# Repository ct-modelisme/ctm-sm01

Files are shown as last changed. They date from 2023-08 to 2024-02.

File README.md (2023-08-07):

# CTM-SM01: Servo-Motors decoder

The CTM-SM01 is a servo-motors electronic controller for modelrailway projects.
This electronic card is compatible with DCC & AC/DC train layouts.

## Licenses

The hardware is released under OpenHardware principes, and the software under OpenSource principes.

 - Hardware (PCB): [Creative Commons Attribution-ShareAlike 4.0 International License](http://creativecommons.org/licenses/by-sa/4.0/)
 - Software (Firmware): [GNU General Public License v3](https://www.gnu.org/licenses/)

## Current releases

 - Hardware (PCB): version 1.3
 - Software (Firmware): version 1.2

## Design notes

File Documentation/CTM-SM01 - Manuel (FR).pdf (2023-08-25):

# CTM-SM01

## Commande de servo-moteurs

La carte CTM-SM01 est une carte de commande pour 2 aiguillages actionnés par servo-moteur. Elle peut également être utilisée pour commander des signaux mécaniques ou passages à niveau là aussi actionnés par servo-moteur.
En cas de bogue, ou simplement si vous avez des suggestions, merci de me contacter à l’adresse : cyrille.toulet@linux.com

## Fonctionnalités

- Commande par DCC ou par boutons poussoirs (déportés ou non) ;
- 2 voies avec commandes et adresses DCC distinctes ;
- Relais pour réalimentation du cœurs d’aiguillage + option (TCO, rétro-signalisation, etc.) ;
- Fonctionnalité d’apprentissage manuel des débuts et fins de courses ;
- Fonctionnalité d’apprentissage dynamique des adresses DCC ;
- Connexion USB série 115 200 bauds (optionnelle).
https://www.ct-modelisme.fr/ | CTM-SM01 | PCB 1.3 – Firmware 1.2
| Page 1 | Révision : 25 août 2023

## Montage

## Aperçu du montage minimal

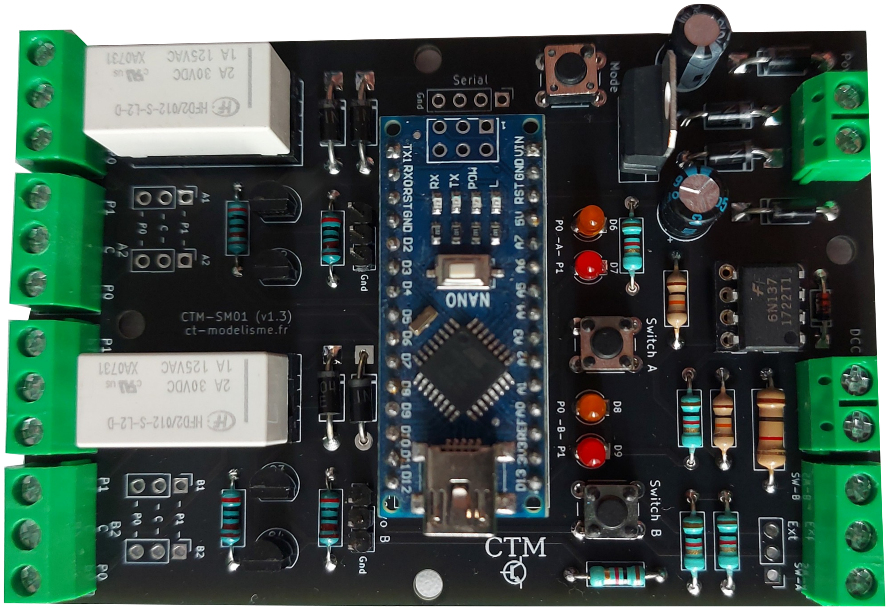
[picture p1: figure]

https://www.ct-modelisme.fr/ | CTM-SM01 | PCB 1.3 – Firmware 1.2
| Page 2 | Révision : 25 août 2023

## Liste des composants

Référence | Qté | Valeur | Type / Boitier / Pas | Autre
A1 | 1 | Arduino Nano
C1 | 1 | Condensateur 220µF / 25V | Radial / D=6.3mm / P=2.5mm
C2 | 1 | Condensateur 220µF / 16V | Radial / D=6.3mm / P=2.5mm
D1, D2, D3, D4, D10, D11, D12, D13 | 8 | Diode 1N4007
D5 | 1 | Diode 1N4148
D6, D8 | 2 | LED verte | 3mm | Ou n’importe quelle autre couleur
D7, D9 | 2 | LED rouge | 3mm | Ou n’importe quelle autre couleur
J1, J2 | 2 | Bornier à vis 1x2 | P=5.08mm
J3, J8, J9, J10, J11 | 5 | Bornier à vis 1x3 | P=5.08mm | Optionnel (si utilisation de J4, J12, J13, J14, J15)
J5 | 1 | Connecteur tulipe 1x4 broches | P=2.54mm | Optionnel (non implémenté pour le moment)
J4, J12, J13, J14, J15 | 5 | Connecteur tulipe 1x3 broches | P=2.54mm | Optionnel (si utilisation de J3, J8, J9, J10, J11)
J6, J7 | 2 | Connecteur 1x3 broches pour servo-moteur | P=2.54mm
K1, K2 | 2 | Relai bistable HFD2 012-S-L2
Q1, Q2, Q3, Q4 | 4 | Transistor BC547 | TO-92
R1 | 1 | Résistance 1k / 1W
R5, R6 | 2
R2, R3, R4, R7, R8 | 5
R9, R10, R11, R12 | 4
SW1, SW2, SW3 | 3 | Bouton poussoir à souder | 6mm
U1 | 1 | Opto-coupleur 6N137 | DIP-8
U2 | 1 | Régulateur de tension LM7805 | TO-220
PCB | 1 | Circuit imprimé CTM-SM01
Options recommandées | Qté | Valeur | Type / Boitier / Pas | Autre
A1 | 2 | Connecteur femelle 15 broches
K1, K2 | 2 | Support de CI 2x8 broches | DIP-16
U1 | 1 | Support de CI 2x4 broches | DIP-8

Résistance 10k / 0.25W
Résistance 1k / 0.25W
Résistance 2.2k / 0.25W

## Ordre de montage recommandé

Comme pour n’importe quel circuit électronique, faites attention au sens des composants (tous sauf les résistances) et commencez des composants les moins hauts pour terminer sur les plus hauts : diode 1N4148 (D5), puis résistances 1/4 W (toutes sauf R1), puis diodes 1N4007 (D1 à D4 et D10 à D13) et résistance 1W (R1). Ensuite, boutons poussoirs (SW1-3), supports de CI (s’il y en a), opto-coupleur (U1), LEDs, transistors BC547 (Q1 à Q4), connecteurs et borniers à vis, condensateurs 220µF (C1 et C2), relais (K1 et K2) et enfin, le régulateur de tension 5V (U2).

Aide complémentaire : si vous doutez du sens des LEDs, c’est la cathode (le côté plat de l’arrondi de la LED, qui est également le côté de la patte la plus courte) qui se trouve vers les écritures D5 à D9. Pour les transistors Q1 à Q4, faites bien attention de ne pas souder plusieurs pattes ensemble, car elles sont assez rapprochées. Enfin, faites bien attention lors de l’enfichage de l’opto-coupleur U1 et de l’arduino A1 de ne pas plier de patte.

## Options

En fonction du câblage de votre réseau, vous pouvez opter pour presque chaque entrée/sortie entre tiliser un bornier, utiliser un connecteur tulippe ou à broche, ou encore souder des fils directement à la place du connecteur.
Ainsi, les connecteurs J3 et J4 sont reliés, ainsi que J8 avec J12, J9 avec J13, J10 avec J14, et J11 avec J15.
Pour rendre démontable les relais ou l’arduino, vous pouvez également ajouter les supports femelles préconisés dans la liste des compostants.
https://www.ct-modelisme.fr/ | CTM-SM01 | PCB 1.3 – Firmware 1.2
| Page 4 | Révision : 25 août 2023

## Installation

## Firmware

Pour télécharger le dernier firmware de la carte CTM-SM01, rendez-vous sur le site, rubrique
« Téléchargements » : https://ct-modelisme.fr/
Compilez et envoyez le firmware de la carte vers un arduino nano à partir de du logiciel Arduino SDK. Puis enfichez l’arduino sur le connecteur A1.

## Fixation

La carte électronique dispose de 4 trous de montage M3 pour être fixée avec des vis ou des supports édhésifs.

## Connexions

- Connectez une alimentation de 12 à 15V DC sur le connecteur « Power » (peu importe la polarité).
- Connectez ensuite le bus JK sur le connecteur « DCC » (pas de polarité particulière non plus).
- Connectez le servo-moteur de l’aiguillage A sur le connecteur J6 (inscription « Servo A ») et le servo-moteur de l’aiguillage B sur le connecteur J7 (inscription « Servo B »).
Astuce : L’inscription « Gnd » correspond au fil de masse (généralement le fil marron ou noir) du servo-moteur.
- Si vous avez des boutons poussoirs de commande déportés (par exemple ceux d’un TCO), connectez les sur un des connecteurs SW-A / Ext / SW-B.
- Enfin, connectez votre cœur d’aiguille sur un commun (A1-C, ou A2-C, ou B1-C, ou B2-C) et le bus JK qui alimente l’aiguille sur les bornes correspondantes (ex : A1-P0 et A1-P1 si A1-C, ou A2-P0 et A2-P1 si A2-C, ou B1-P0 et B1-P1 si B1-C, ou B2-P0 et B2-P1 si B2-C).
- Le second contact de chaque relai peut être utilisé par exemple pour de la rétro-signalisation, ou pour alimenter des signaux de voie.
https://www.ct-modelisme.fr/ | CTM-SM01 | PCB 1.3 – Firmware 1.2
| Page 5 | Révision : 25 août 2023

## Aide visuelle

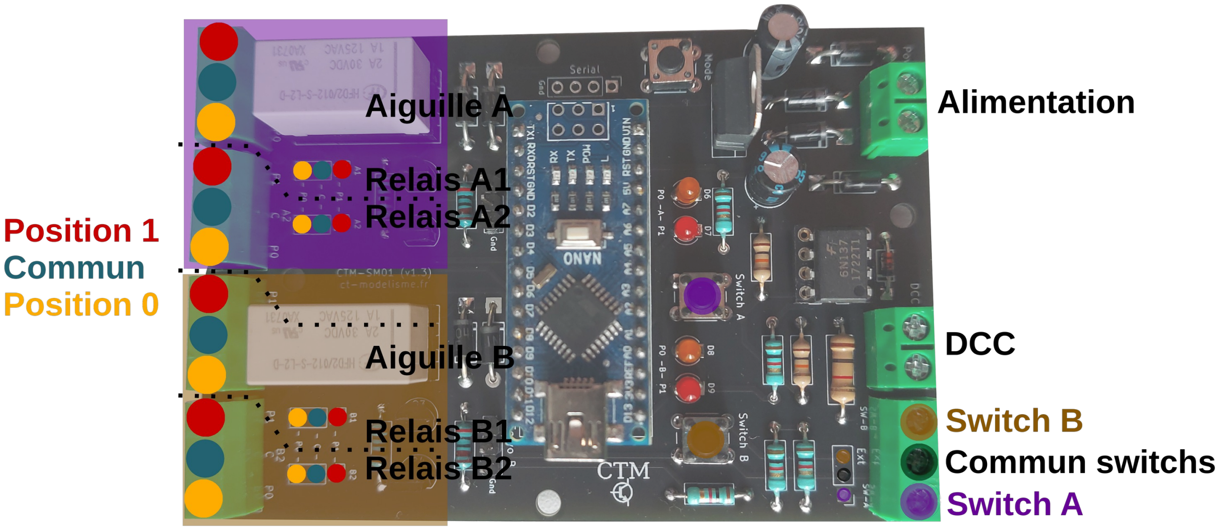
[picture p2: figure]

## Utilisation

## Apprentissage d’adresse DCC

Pour entrer en mode apprentissage d’adresse, appuyez 3 secondes sur le bouton « Mode ». La LED « L » de l’arduino s’allume.
Envoyez une commande d’accessoire sur la première adresse voulue depuis votre centrale DCC. Cette adresse sera mémorisée par la carte comme adresse DCC de l’aiguillage A.
Ensuite, envoyez une nouvelle commande d’accessoire sur la seconde adresse voulue. Cette seconde adresse sera mémorisée par la carte comme adresse DCC de l’aiguillage B.
Une fois les deux adresses apprises, la carte repasse en mode normal et la LED « L » de l’arduino s’éteint.
Astuce : vous pouvez quitter à tout moment le mode apprentissage en appuyant 2 secondes sur le bouton « Mode ».

## Réglage de début et fin de course des servo-moteurs

Pour entrer en mode apprentissage des positions, appuyez 2 secondes sur le bouton « Mode », puis sans le relacher, appuyez 2 secondes sur le bouton «Switch A ». Relâchez « Switch A » puis relachez « Mode ».
La première LED clignote. Vous allez régler la position de début de course du servo-moteur de l’aiguillage A en restant appuyé sur le bouton « Switch A » ou « Switch B ». Le servo-moteur se déplace en temps réel.
Une fois la position de début de course de l’aiguillage A réglée, appuyez 1 seconde sur le bouton « Mode ».
La seconde LED clignote. Vous allez régler la position de fin de course du servo-moteur de l’aiguillage A de la même manière que précédement.
Une fois la position de fin de course de l’aiguilage A réglée, appuyez 1 seconde sur le bouton « Mode ».
La troisième LED clignote, indiquant la configuration du début de course de l’aiguillage B. Procédez au réglage de la même manière que précédement.
Une fois la position de début de course de l’aiguillage B réglée, appuyez 1 seconde sur le bouton « Mode ».
La quatrième LED clignote, indiquant finalement la configuration de fin de course du servo-moteur de l’aiguillage B.
Une fois le réglage terminé, appuyez 1 seconde sur le bouton « Mode » pour revenir en
https://www.ct-modelisme.fr/ | CTM-SM01 | PCB 1.3 – Firmware 1.2
| Page 7 | Révision : 25 août 2023

fonctionnement normal.

## Moniteur série & réinitialisation de la carte

Lorsque vous branchez un câble USB à l’arduino, et que vous lancez le moniteur série à 115 200 bauds, un appuis court sur le bouton « Mode » imprimera la configuration courante de la carte. Différentes informations seront affichée suite à plusieurs appuis sur le bouton « Mode », jusqu’à revenir en fonctionnement normal.
Astuce : lors que vous utilisez le moniteur série, il est possible de réinitialiser la carte en tapant la commande « reset » dans la console. Cette commande aura pour effet de réinitialiser la carte à ses paramètres d’usine.

## Changement d’état d’un aiguillage

L’état des aiguillages A et B sont indiqués par les couples de LED D6/D7 et D8/D9.
Pour basculer un aiguillage de l’état 0 à l’état 1, il suffit d’appuyer sur le bouton correspondant
(« Switch A » pour l’aiguillage A ou « Switch B » pour l’aiguillage B) ou d’envoyer l’ordre DCC à l’adresse programmée.
Lors du changement d’état, la LED courante s’éteint, le servo-moteur effectue son déplacement, puis la nouvelle LED s’allume. Le relais correspondant à l’aiguillage est basculé à mi-chemin de la course du servo-moteur.
Astuce : il es possible de déporter les boutons « Switchs A » et « Switch B », par exemple sur un TCO, avec les connecteurs J3 ou J4.

## Liste des CVs

CV(s) | Description | Valeur d’usine
1 et 9 | Adresse longue – Aiguillage A | 3 et 0 (adresse 3)
47 et 48 | Adresse longue – Aiguillage B | 4 et 0 (adresse 4)
49 et 50 | Première position – Servo aiguilalge A | 80 et 0 (80 °)
51 et 52 | Dernière position – Servo aiguilalge A | 120 et 0 (120°)
53 et 54 | Première position – Servo aiguilalge B | 80 et 0 (80 °)
55 et 56 | Dernière position – Servo aiguilalge B | 120 et 0 (120°)
57 | Durée d’alimentation des relais | 75 (75 ms)
58 | Attente entre chaque mouvement de servo | 50 (50 ms)
112 | État mémorisé de l’aiguillage A | 0
113 | État mémorisé de l’aiguillage B | 0
https://www.ct-modelisme.fr/ | CTM-SM01 | PCB 1.3 – Firmware 1.2
| Page 8 | Révision : 25 août 2023

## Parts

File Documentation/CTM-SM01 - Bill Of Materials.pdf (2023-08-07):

CTM-SM01 (EN)

Page 1

Reference | Quantity | Value | Type / Case / Spacing | Other
A1 | 1 | Arduino Nano
C1 | 1 | 220µF / 25V | Radial / D=6.3mm / P=2.5mm
C2 | 1 | 220µF / 16V | Radial / D=6.3mm / P=2.5mm
D1, D2, D3, D4, D10, D11, D12, D13 | 8 | 1N4007
D5 | 1 | 1N4148
D6, D8 | 2 | Green LED | 3mm | Or any other color
D7, D9 | 2 | Red LED | 3mm | Or any other color
J1, J2 | 2 | Terminal screw 1x2 | P=5.08mm
J3, J8, J9, J10, J11 | 5 | Terminal screw 1x3 | P=5.08mm | Optional (if use of J4, J12, J13, J14, J15)
J5 | 1 | Conn 1x4 pins | P=2.54mm | Optional (not implemented yet)
J4, J12, J13, J14, J15 | 5 | Conn 1x3 pins | P=2.54mm | Optional (if use of J3, J8, J9, J10, J11)
J6, J7 | 2 | Conn 1x3 pins for servos | P=2.54mm
K1, K2 | 2 | Relay HFD2 012-S-L2
Q1, Q2, Q3, Q4 | 4 | BC547 | Inline / TO-92
R1 | 1 | 1k / 1W
R5, R6 | 2 | 10k / 0.25W
R2, R3, R4, R7, R8 | 5 | 1k / 0.25W
R9, R10, R11, R12 | 4 | 2.2k / 0.25W
SW1, SW2, SW3 | 3 | Embeded push button | 6mm
U1 | 1 | 6N137 | DIP-8
U2 | 1 | LM7805 | TO-220
PCB | 1 | CTM-SM01
Recommended options | Quantity | Value | Type / Case / Spacing | Other
A1 | 2 | 15 pins fem connector
K1, K2 | 2 | 2x8 pins IC support | DIP-16
U1 | 1 | 2x4 pins IC support | DIP-8

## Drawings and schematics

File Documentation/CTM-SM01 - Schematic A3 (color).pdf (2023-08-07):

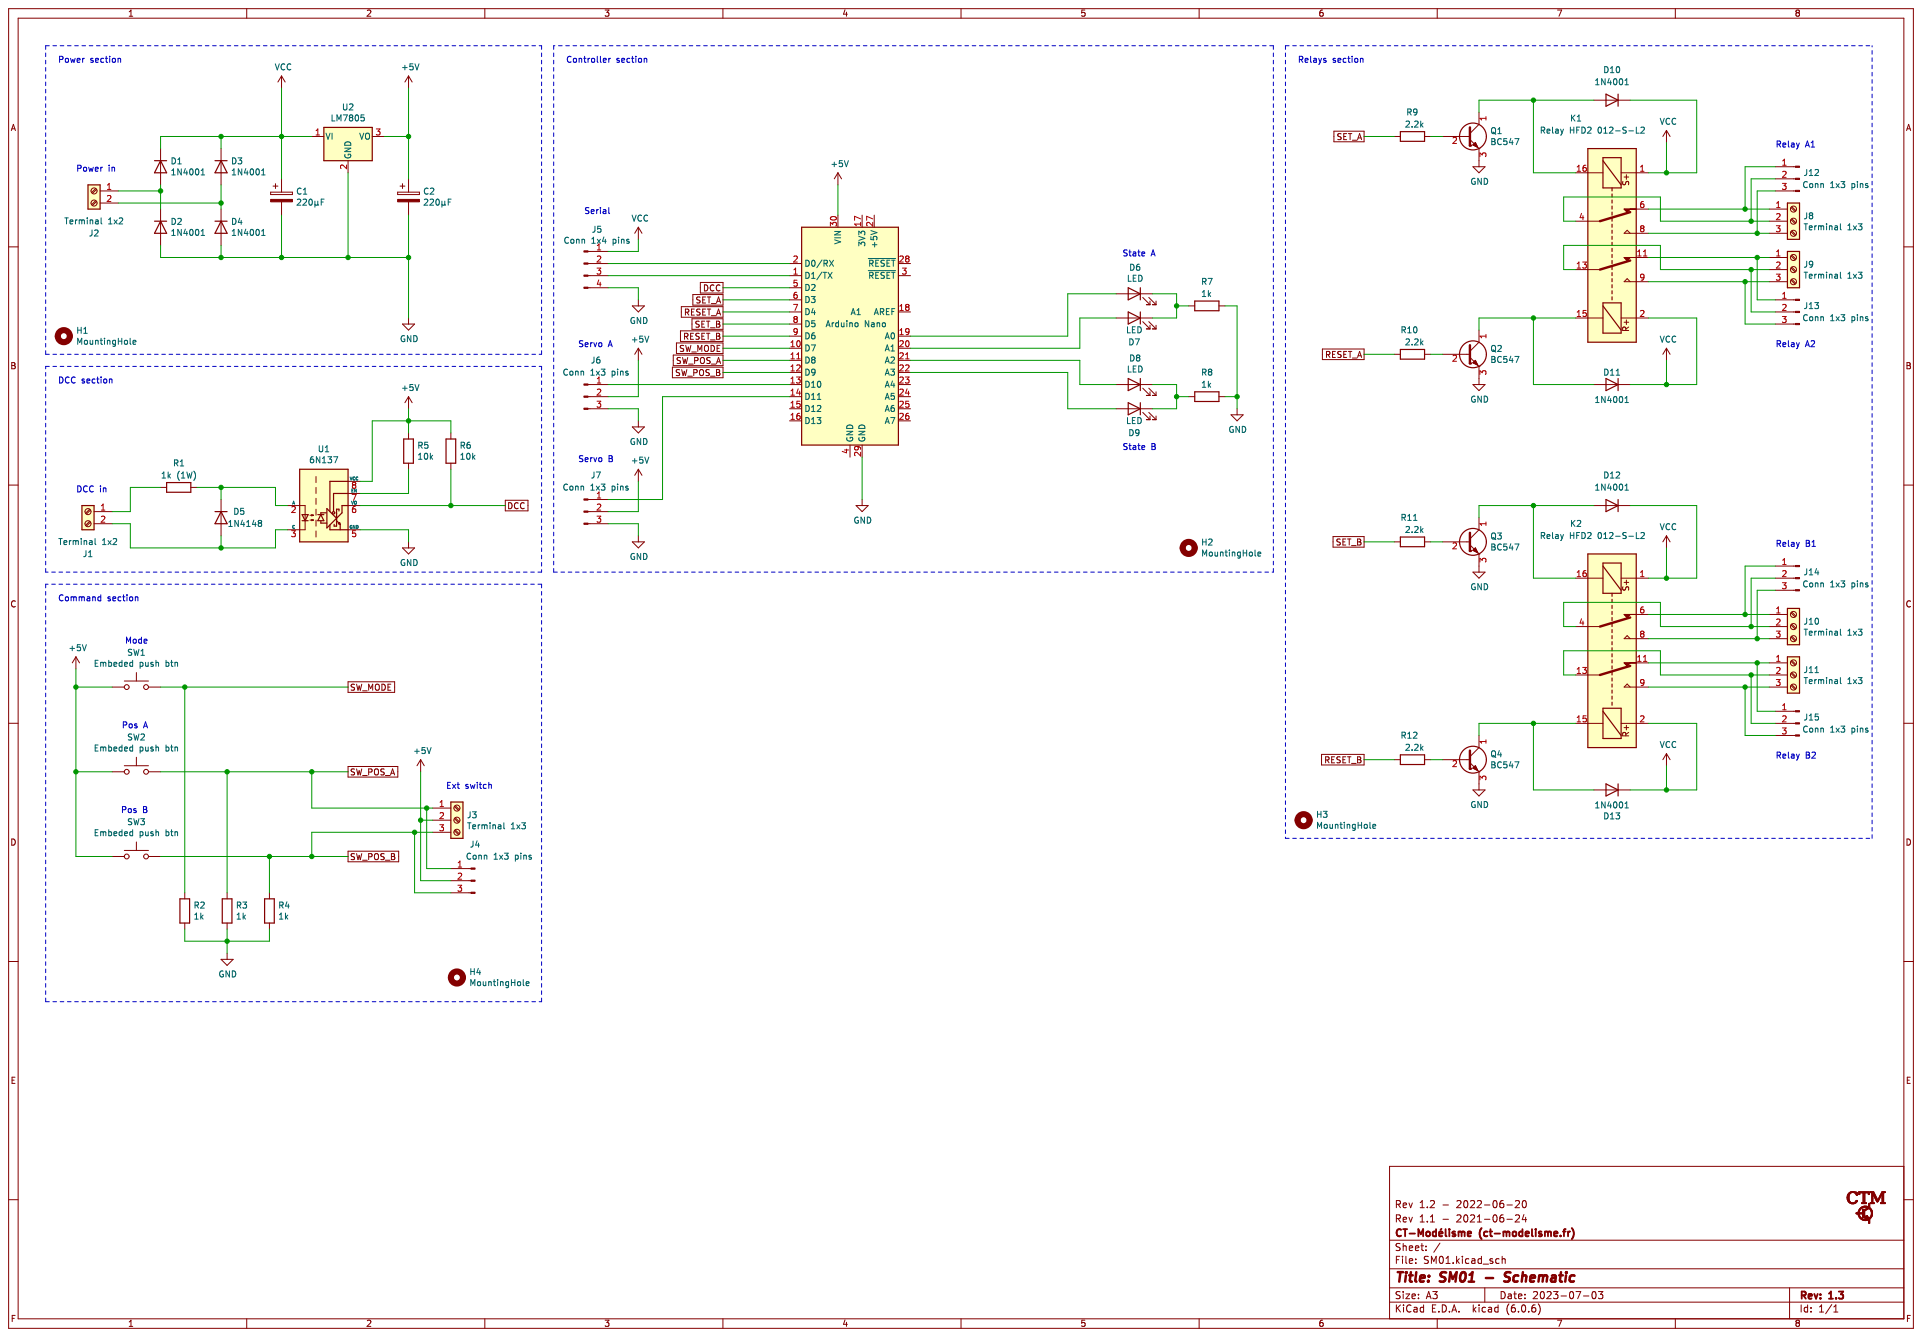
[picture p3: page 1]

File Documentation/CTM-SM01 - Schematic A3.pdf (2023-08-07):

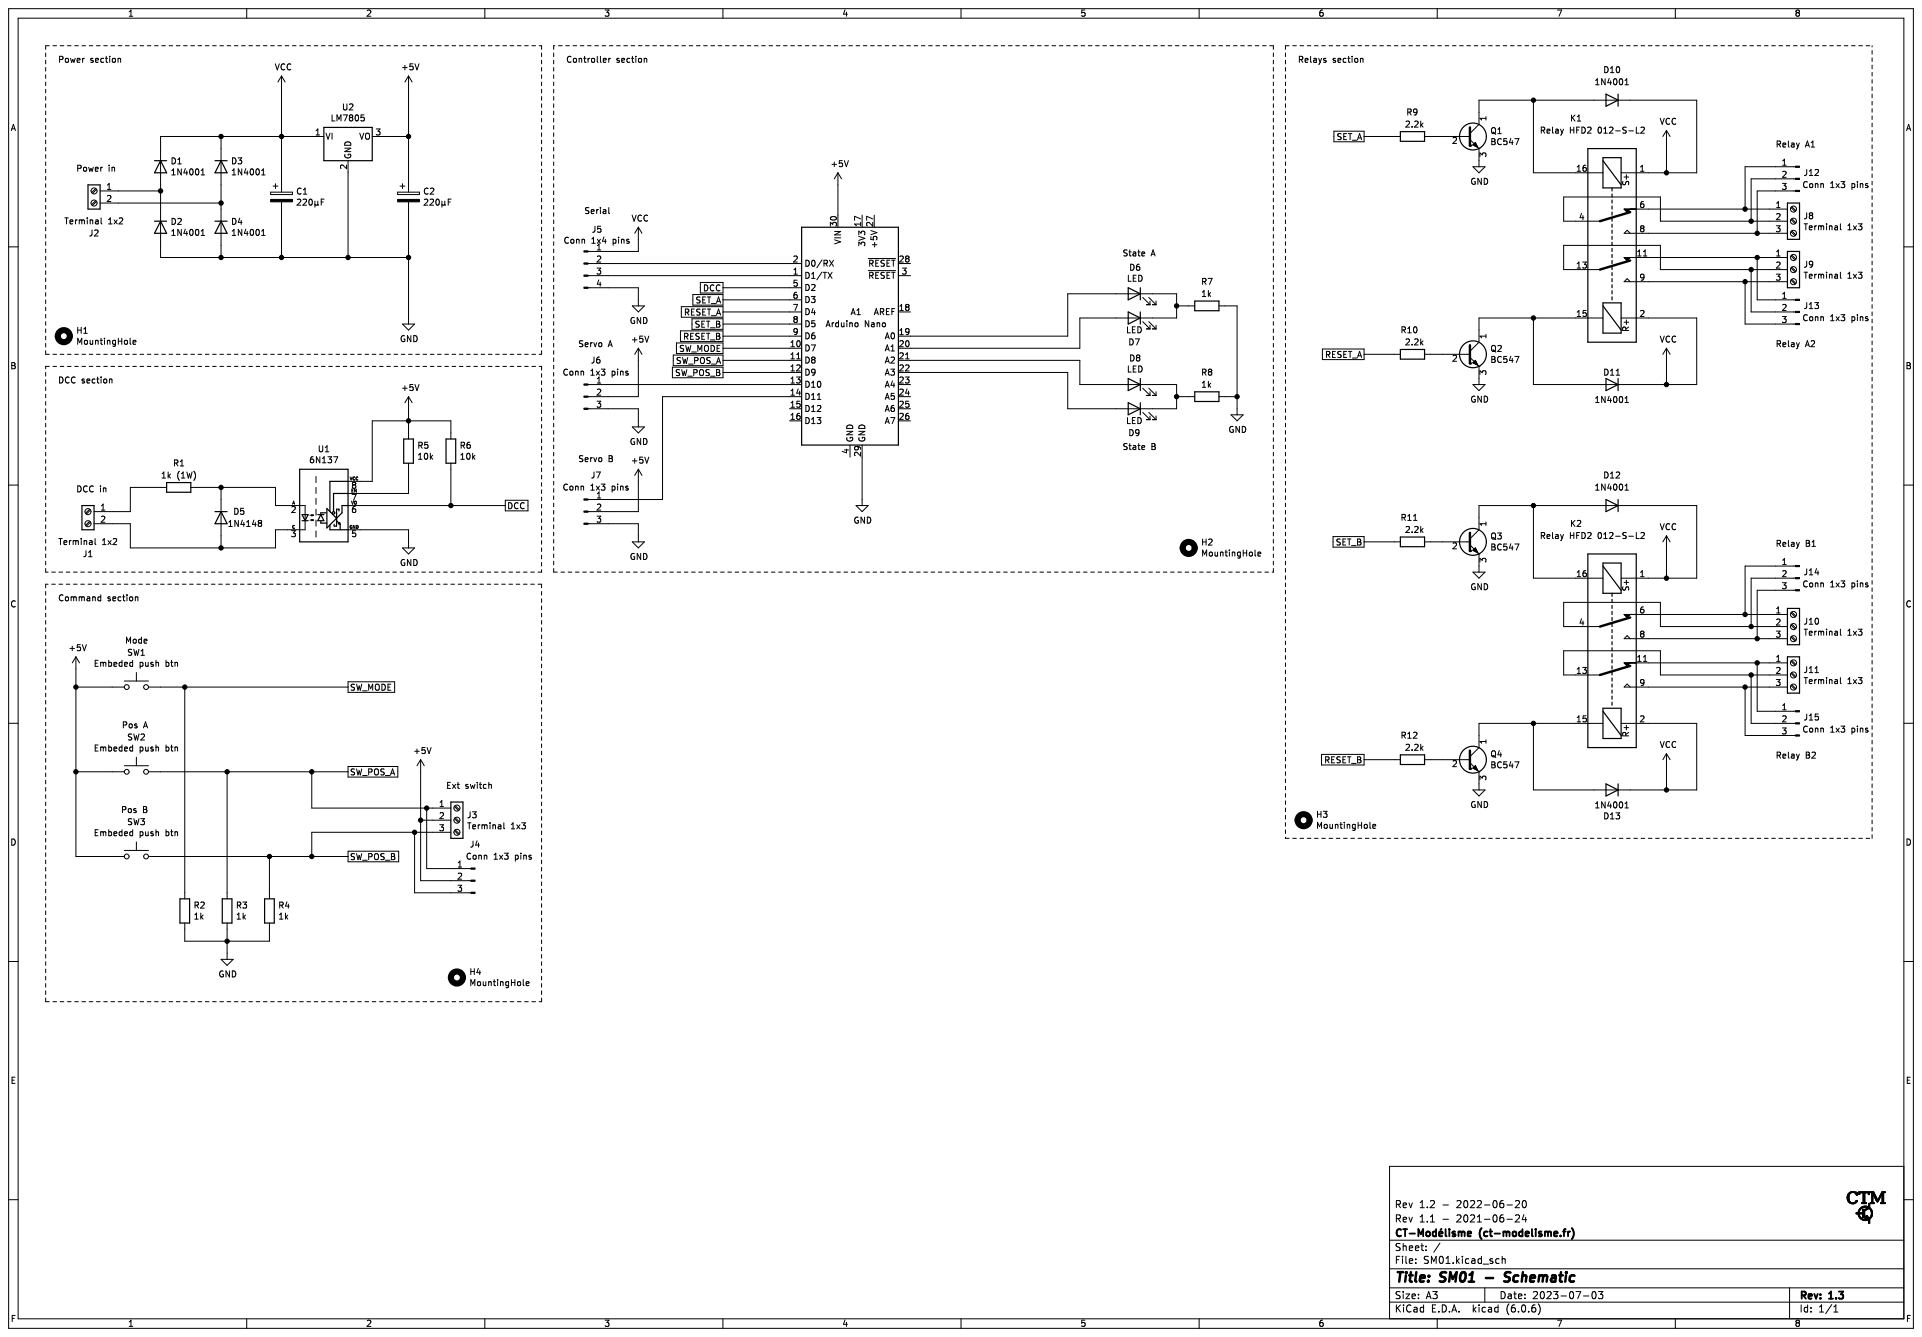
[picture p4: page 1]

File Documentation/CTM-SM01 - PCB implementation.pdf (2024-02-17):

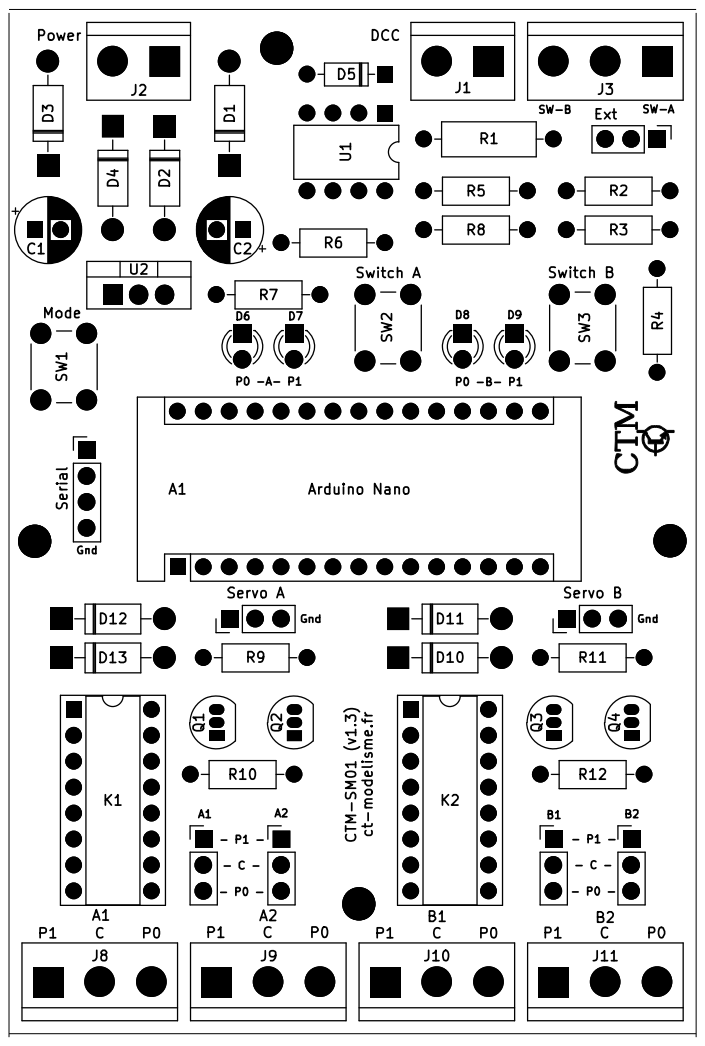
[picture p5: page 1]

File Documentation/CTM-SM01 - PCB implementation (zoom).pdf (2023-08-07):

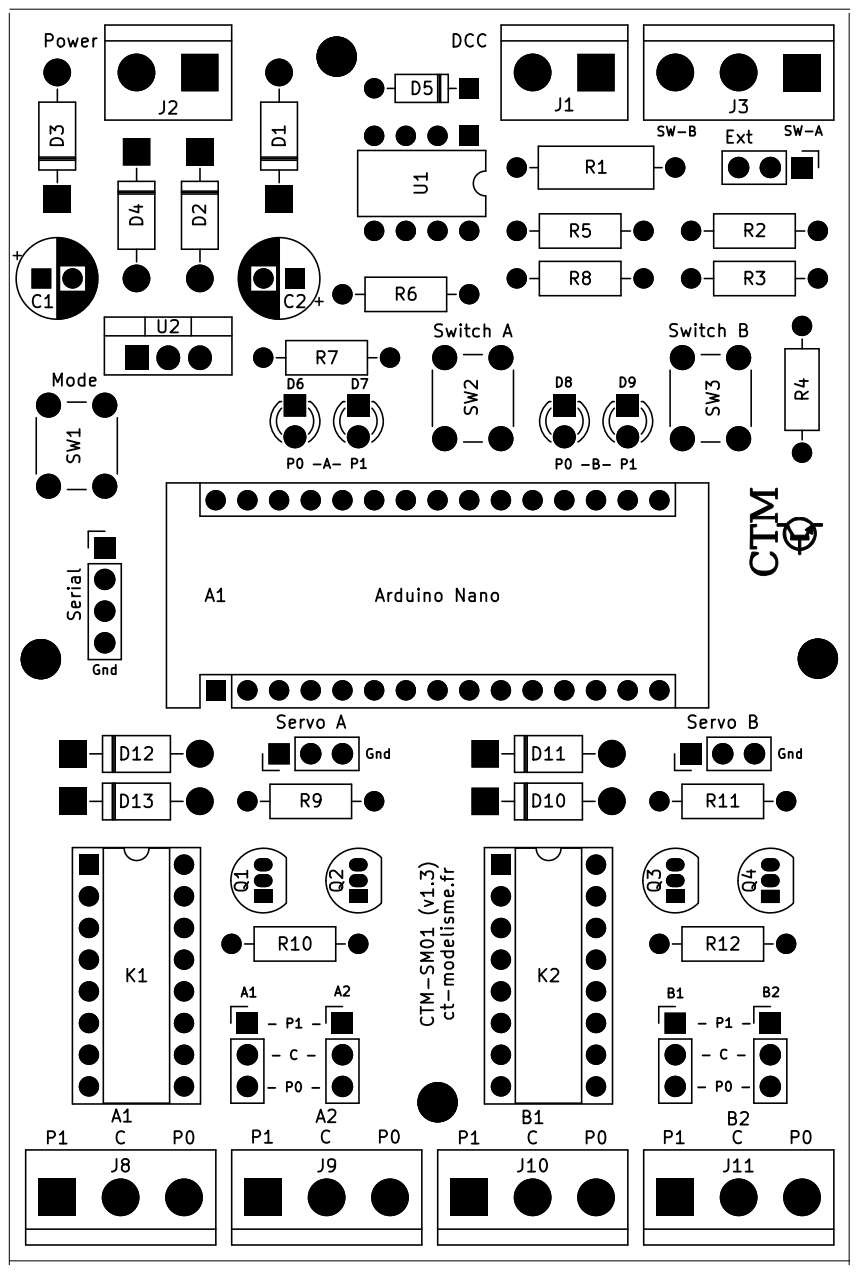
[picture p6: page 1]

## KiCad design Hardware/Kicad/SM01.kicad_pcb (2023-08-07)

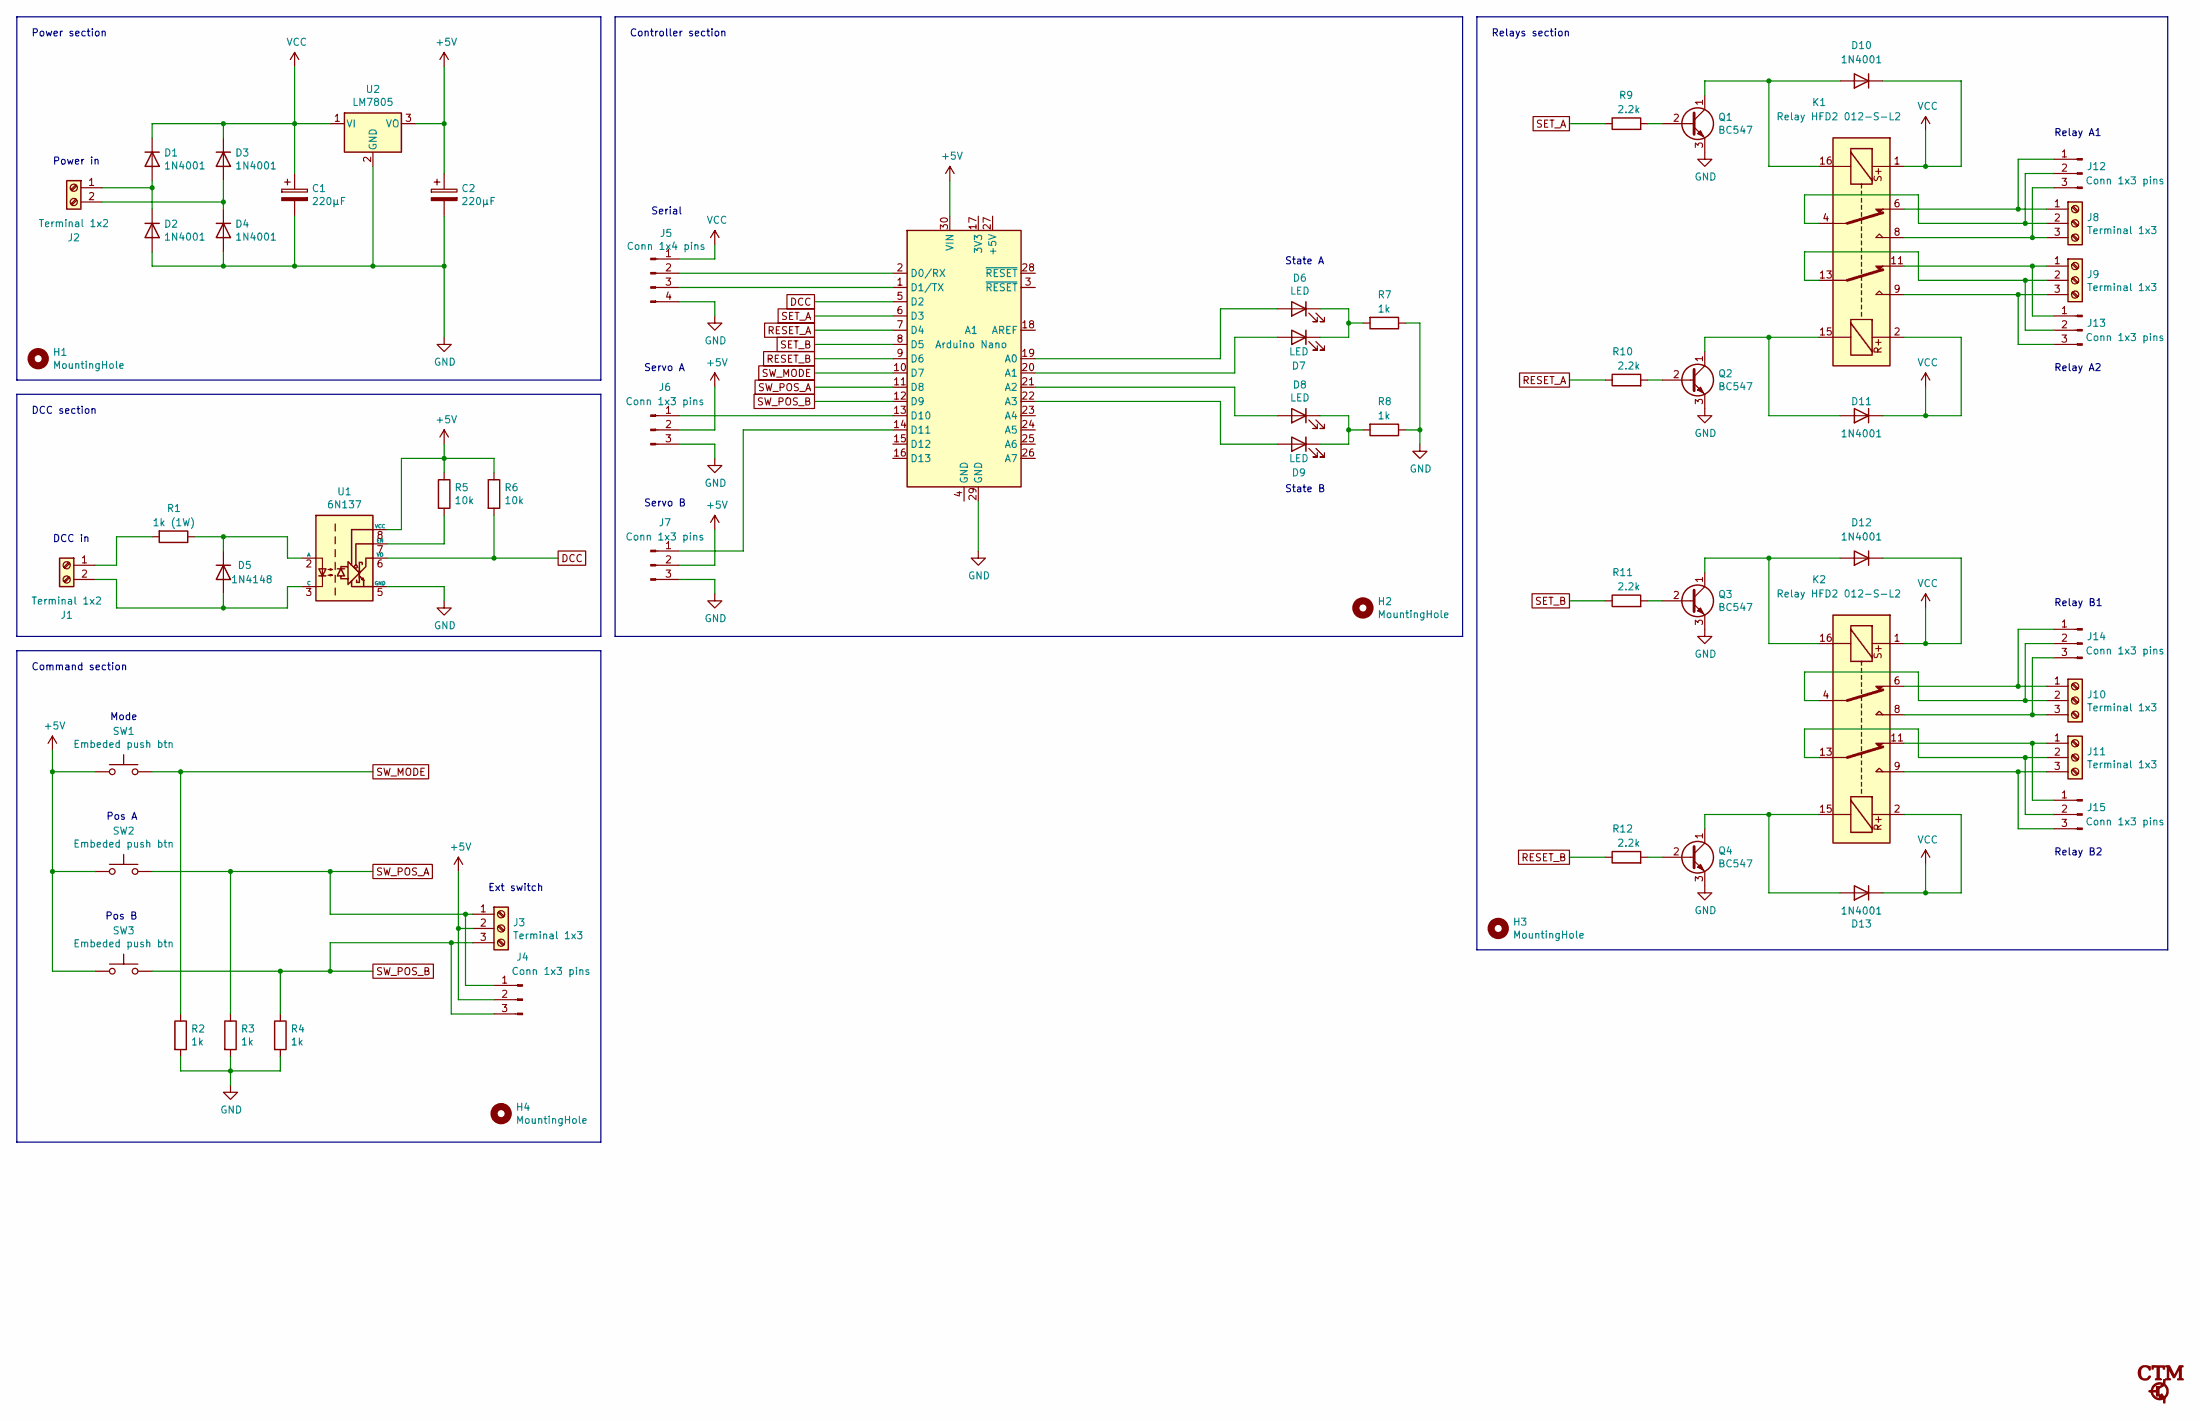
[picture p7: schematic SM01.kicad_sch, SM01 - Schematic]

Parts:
A1: Arduino Nano; Arduino_Nano
C1, C2: 220µF; CP_Radial_D6.3mm_P2.50mm
D1, D2, D3, D4, D10, D11, D12, D13: 1N4001; D_DO-41_SOD81_P10.16mm_Horizontal
D5: 1N4148; D_DO-35_SOD27_P7.62mm_Horizontal
D6, D7, D8, D9: LED; LED_D3.0mm
H1, H2, H3, H4: MountingHole; MountingHole_3.2mm_M3
J1, J2: Terminal 1x2; TerminalBlock_bornier-2_P5.08mm
J3, J8, J9, J10, J11: Terminal 1x3; TerminalBlock_bornier-3_P5.08mm
J4, J6, J7, J12, J13, J14, J15: Conn 1x3 pins; PinHeader_1x03_P2.54mm_Vertical
J5: Conn 1x4 pins; PinHeader_1x04_P2.54mm_Vertical
K1, K2: Relay HFD2 012-S-L2; DIP-16_W7.62mm_Socket
Q1, Q2, Q3, Q4: BC547; TO-92_Inline
R1: 1k (1W); R_Axial_DIN0309_L9.0mm_D3.2mm_P12.70mm_Horizontal
R2, R3, R4, R7, R8: 1k; R_Axial_DIN0207_L6.3mm_D2.5mm_P10.16mm_Horizontal
R5, R6: 10k; R_Axial_DIN0207_L6.3mm_D2.5mm_P10.16mm_Horizontal
R9, R10, R11, R12: 2.2k; R_Axial_DIN0207_L6.3mm_D2.5mm_P10.16mm_Horizontal
SW1, SW2, SW3: Embeded push btn; SW_PUSH_6mm
U1: 6N137; DIP-8_W7.62mm
U2: LM7805; TO-220-3_Vertical

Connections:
+5V: A1.30 (VIN), C2.1, J3.2, J4.2, J6.2, J7.2, R5.1, R6.1, SW1.1, SW2.1, SW3.1, U1.8 (VCC), U2.3 (VO)
DCC: A1.5 (D2), R6.2, U1.6 (VO)
GND: A1.29 (GND), C1.2, C2.2, D2.2 (A), D4.2 (A), J5.4, J6.3, J7.3, Q1.3 (E), Q2.3 (E), Q3.3 (E), Q4.3 (E), R2.2, R3.2, R4.2, R7.1, R8.1, U1.5 (GND), U2.2 (GND)
unnamed: A1.1 (D1/TX), J5.3
unnamed: A1.2 (D0/RX), J5.2
unnamed: A1.13 (D10), J6.1
unnamed: A1.14 (D11), J7.1
unnamed: A1.19 (A0), D6.2 (A)
unnamed: A1.20 (A1), D7.2 (A)
unnamed: A1.21 (A2), D8.2 (A)
unnamed: A1.22 (A3), D9.2 (A)
unnamed: D1.2 (A), D2.1 (K), J2.1
unnamed: D3.2 (A), D4.1 (K), J2.2
unnamed: D5.1 (K), R1.1, U1.2 (A)
unnamed: D5.2 (A), J1.2, U1.3 (C)
unnamed: D6.1 (K), D7.1 (K), R7.2
unnamed: D8.1 (K), D9.1 (K), R8.2
unnamed: D10.2 (A), K1.16, Q1.1 (C)
unnamed: D11.2 (A), K1.15, Q2.1 (C)
unnamed: D12.2 (A), K2.16, Q3.1 (C)
unnamed: D13.2 (A), K2.15, Q4.1 (C)
unnamed: J1.1, R1.2
unnamed: J10.1, J14.1, K2.6
unnamed: J10.2, J14.2, K2.4
unnamed: J10.3, J14.3, K2.8
unnamed: J11.1, J15.1, K2.11
unnamed: J11.2, J15.2, K2.13
unnamed: J11.3, J15.3, K2.9
unnamed: J8.1, J12.1, K1.6
unnamed: J8.2, J12.2, K1.4
unnamed: J8.3, J12.3, K1.8
unnamed: J9.1, J13.1, K1.11
unnamed: J9.2, J13.2, K1.13
unnamed: J9.3, J13.3, K1.9
unnamed: Q1.2 (B), R9.2
unnamed: Q2.2 (B), R10.2
unnamed: Q3.2 (B), R11.2
unnamed: Q4.2 (B), R12.2
unnamed: R5.2, U1.7 (EN)
RESET_A: A1.7 (D4), R10.1
RESET_B: A1.9 (D6), R12.1
SET_A: A1.6 (D3), R9.1
SET_B: A1.8 (D5), R11.1
SW_MODE: A1.10 (D7), R2.1, SW1.2
SW_POS_A: A1.11 (D8), J3.1, J4.1, R3.1, SW2.2
SW_POS_B: A1.12 (D9), J3.3, J4.3, R4.1, SW3.2
VCC: C1.1, D1.1 (K), D3.1 (K), D10.1 (K), D11.1 (K), D12.1 (K), D13.1 (K), J5.1, K1.1, K1.2, K2.1, K2.2, U2.1 (VI)

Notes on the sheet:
Relay B2
Command section
Power section
Relay B1
Pos B
Power in
Mode
Relay A2
Controller section
State A
State B
Servo A
DCC in
Relays section
Ext switch
Serial
Servo B
Pos A
Relay A1
DCC section

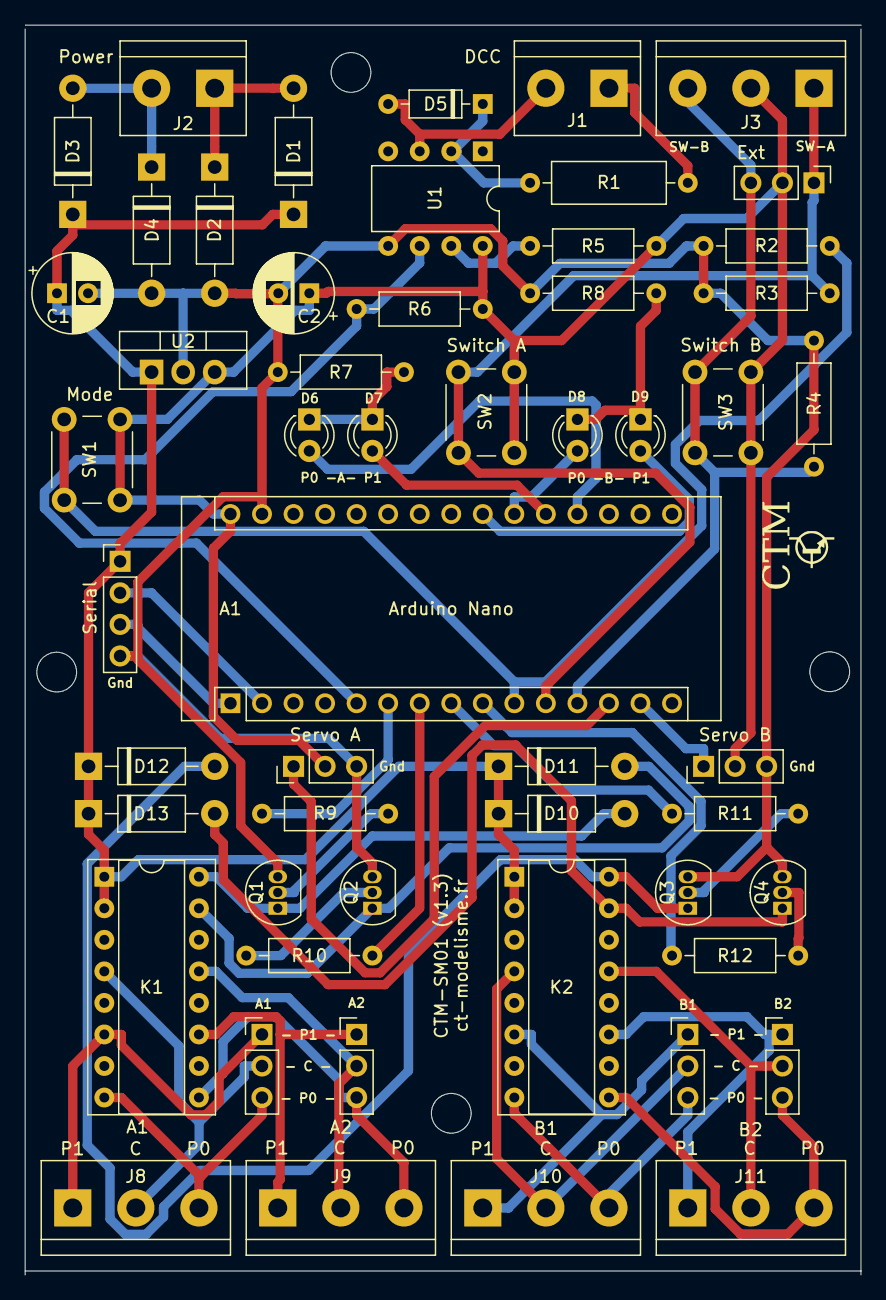
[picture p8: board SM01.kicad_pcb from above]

Board: 2 copper layers, 67.3 x 100.6 mm, 58 parts (0 on the bottom side), 47 nets.

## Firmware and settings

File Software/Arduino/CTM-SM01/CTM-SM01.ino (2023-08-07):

/**
 * CT-Modelisme (ct-modelisme.fr) - Decodeur Servo-Moteur 01 (CTM-SM01.ino)
 * 
 * Requires NmraDcc library from mrrwa (https://github.com/mrrwa/NmraDcc)
 * Requires Servo library from arduino project (https://www.arduino.cc/reference/en/libraries/servo/)
 * 
 * 
 * Copyright (C) 2021 Cyrille TOULET
 *
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
 * 
 * Cyrille TOULET <cyrille.toulet@linux.com>
 * Thu 22 Jul 10:20:42 CEST 2021
 */

#include "DCCInterface.h"
#include "AccessoryDecoder.h"
#include "CLI.h"


// Objects
CLI *cli;
DCCInterface *dcc;
AccessoryDecoder *decoder;


// Setup arduino
void setup()
{
  // Command line interface
  cli = CLI::getInstance();
  cli->setup();

  // DCC
  dcc = DCCInterface::getInstance();
  dcc->setup();

  // Accessory decoder
  decoder = AccessoryDecoder::getInstance();
  decoder->setup();
}


// Run main loop
void loop()
{
  cli->loop();
  decoder->loop();
  dcc->loop();
}

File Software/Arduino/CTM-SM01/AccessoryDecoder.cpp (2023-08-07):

/**
 * CT-Modelisme (ct-modelisme.fr) - Decodeur Servo-Moteur 01 (CTM-SM01.ino)
 *
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
 * 
 * Cyrille TOULET <cyrille.toulet@linux.com>
 * Thu 22 Jul 10:20:42 CEST 2021
 */

#include "AccessoryDecoder.h"


// The factory CV values for this decoder
CV factoryCVs [] =
{
  {CV_ACCESSORY_DECODER_ADDRESS_LSB, 3},      // Less signifiant bits of long address 1
  {CV_ACCESSORY_DECODER_ADDRESS_MSB, 0},      // Most signifiant bits of long address 1
  {CV_ACCESSORY_DECODER_ADDRESS_2_LSB, 4},    // Less signifiant bits of long address 2
  {CV_ACCESSORY_DECODER_ADDRESS_2_MSB, 0},    // Most signifiant bits of long address 2
  {CV_ACCESSORY_DECODER_POS_A0_LSB, 80},      // Less signifiant bits of the first position of A servo
  {CV_ACCESSORY_DECODER_POS_A0_MSB, 0},       // Less signifiant bits of the first position of A servo
  {CV_ACCESSORY_DECODER_POS_A1_LSB, 120},     // Less signifiant bits of the end position of A servo
  {CV_ACCESSORY_DECODER_POS_A1_MSB, 0},       // Less signifiant bits of the end position of A servo
  {CV_ACCESSORY_DECODER_POS_B0_LSB, 80},      // Less signifiant bits of the first position of B servo
  {CV_ACCESSORY_DECODER_POS_B0_MSB, 0},       // Less signifiant bits of the first position of B servo
  {CV_ACCESSORY_DECODER_POS_B1_LSB, 120},     // Less signifiant bits of the end position of B servo
  {CV_ACCESSORY_DECODER_POS_B1_MSB, 0},       // Less signifiant bits of the end position of B servo
  {CV_ACCESSORY_DECODER_RELAY_PULSE, 75},     // The pulse duration to switch relays
  {CV_ACCESSORY_DECODER_SERVO_DELAY, 50},     // The delay between each servo step
  {CV_ACCESSORY_DECODER_STATE_A, 0},          // The state of A servo
  {CV_ACCESSORY_DECODER_STATE_B, 0},          // The state of B servo
};


/**
 * Generic constructor for AccessoryDecoder
 */
AccessoryDecoder::AccessoryDecoder() 
{
  this->dcc = DCCInterface::getInstance();
  this->dcc->registerFactoryCVs(*factoryCVs, sizeof(factoryCVs) / sizeof(CV));
  
  this->mode = AccessoryDecoder::RUNNING;
  this->posProgRequested = 0;
  this->waitForSecondAddress = 0;
  this->timerRunning = 0;
  
  // Read settings from decoder CVs
  this->dccAddressA = this->dcc->readIntFromCVs(CV_ACCESSORY_DECODER_ADDRESS_LSB, CV_ACCESSORY_DECODER_ADDRESS_MSB);
  this->dccAddressB = this->dcc->readIntFromCVs(CV_ACCESSORY_DECODER_ADDRESS_2_LSB, CV_ACCESSORY_DECODER_ADDRESS_2_MSB);
  this->posA0 = this->dcc->readIntFromCVs(CV_ACCESSORY_DECODER_POS_A0_LSB, CV_ACCESSORY_DECODER_POS_A0_MSB);
  this->posA1 = this->dcc->readIntFromCVs(CV_ACCESSORY_DECODER_POS_A1_LSB, CV_ACCESSORY_DECODER_POS_A1_MSB);
  this->posB0 = this->dcc->readIntFromCVs(CV_ACCESSORY_DECODER_POS_B0_LSB, CV_ACCESSORY_DECODER_POS_B0_MSB);
  this->posB1 = this->dcc->readIntFromCVs(CV_ACCESSORY_DECODER_POS_B1_LSB, CV_ACCESSORY_DECODER_POS_B1_MSB);
  this->stateA = this->dcc->nmraDCC.getCV(CV_ACCESSORY_DECODER_STATE_A);
  this->stateB = this->dcc->nmraDCC.getCV(CV_ACCESSORY_DECODER_STATE_B);

  // Apply saved states
  this->switchStateA(this->stateA);
  this->switchStateB(this->stateB);  
}


/**
 * The deecoder setup function
 */
void 
AccessoryDecoder::setup()
{
  // Set pin modes
  pinMode(MODE_LED_OUT, OUTPUT);
  pinMode(POS_A0_REL_OUT, OUTPUT);
  pinMode(POS_A1_REL_OUT, OUTPUT);
  pinMode(POS_B0_REL_OUT, OUTPUT);
  pinMode(POS_B1_REL_OUT, OUTPUT);
  pinMode(POS_A0_LED_OUT, OUTPUT);
  pinMode(POS_A1_LED_OUT, OUTPUT);
  pinMode(POS_B0_LED_OUT, OUTPUT);
  pinMode(POS_B1_LED_OUT, OUTPUT);
  pinMode(MODE_BTN_IN, INPUT);
  pinMode(A_BTN_IN, INPUT);
  pinMode(B_BTN_IN, INPUT);
  
  // Initialize servos
  this->servoA.attach(SERVO_A_OUT);
  this->servoB.attach(SERVO_B_OUT);



  Serial.println("-- Running mode --");
}


/**
 * The deecoder loop
 */
void 
AccessoryDecoder::loop()
{
  if(this->mode == RUNNING)
  {
    digitalWrite(MODE_LED_OUT, LOW);
    this->defineMode();

    if(digitalRead(A_BTN_IN))
    {
      this->switchStateA(! this->stateA);
      
      // Software anti-rebound
      do {
        delay(200);
      } while(digitalRead(A_BTN_IN));
    }
    
    if(digitalRead(B_BTN_IN))
    {
      this->switchStateB(!this->stateB);
      
      // Software anti-rebound
      do {
        delay(200);
      } while(digitalRead(B_BTN_IN));
    }
  }

  else if(this->mode == ADDR_PROG)
    this->addressProgrammingMode();
    
  else if(this->mode == POS_PROG)
    this->positionProgrammingMode();
    
  else if(this->mode == INFO)
    this->informationMode();
}



/**
 * Switch A to new state
 * 
 * @param state: The new state of A
 */
void
AccessoryDecoder::switchStateA(byte state)
{
  Serial.print("Switching A to state ");
  Serial.print(state);
  Serial.println(".");

  digitalWrite(POS_A0_LED_OUT, LOW);
  digitalWrite(POS_A1_LED_OUT, LOW);
  digitalWrite(POS_A0_REL_OUT, LOW);
  digitalWrite(POS_A1_REL_OUT, LOW);

  if(state)
  {
    int delta = (this->posA1 - this->servoA.read()) / 2;
    for(int i = this->servoA.read(); i < this->posA1 - delta; i++)
    {
      this->servoA.write(i);
      delay(this->dcc->nmraDCC.getCV(CV_ACCESSORY_DECODER_SERVO_DELAY));
    }

    digitalWrite(POS_A1_REL_OUT, HIGH);
    delay(this->dcc->nmraDCC.getCV(CV_ACCESSORY_DECODER_RELAY_PULSE));
    digitalWrite(POS_A1_REL_OUT, LOW);

    for(int i = this->servoA.read(); i < this->posA1; i++)
    {
      this->servoA.write(i);
      delay(this->dcc->nmraDCC.getCV(CV_ACCESSORY_DECODER_SERVO_DELAY));
    }
  }
  else
  {
    int delta = (this->servoA.read() - this->posA0) / 2;
    for(int i = this->servoA.read(); i > this->posA0 + delta; i--)
    {
      this->servoA.write(i);
      delay(this->dcc->nmraDCC.getCV(CV_ACCESSORY_DECODER_SERVO_DELAY));
    }

    digitalWrite(POS_A0_REL_OUT, HIGH);
    delay(this->dcc->nmraDCC.getCV(CV_ACCESSORY_DECODER_RELAY_PULSE));
    digitalWrite(POS_A0_REL_OUT, LOW);
    
    for(int i = this->servoA.read(); i > this->posA0; i--)
    {
      this->servoA.write(i);
      delay(this->dcc->nmraDCC.getCV(CV_ACCESSORY_DECODER_SERVO_DELAY));
    }
  }

  digitalWrite(POS_A0_LED_OUT, !state);
  digitalWrite(POS_A1_LED_OUT, state);

  this->stateA = state;
  delay(this->dcc->nmraDCC.setCV(CV_ACCESSORY_DECODER_STATE_A, state));
}
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

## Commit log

2023-08-07 Release hardware
    [SM01-B_Cu.gbr, SM01-B_Mask.gbr, SM01-Edge_Cuts.gbr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]
2023-08-25 Update documentation of pcb-1.3/firmware-1.2 version
2023-08-25 Hotfix - Add original doc files
    [CTM-SM01 - Bill Of Materials.ods]
2024-02-17 Adding cartridge to PCB implementation

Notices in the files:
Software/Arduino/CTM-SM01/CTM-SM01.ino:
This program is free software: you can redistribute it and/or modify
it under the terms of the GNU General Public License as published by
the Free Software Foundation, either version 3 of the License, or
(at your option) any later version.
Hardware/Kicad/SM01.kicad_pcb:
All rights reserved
